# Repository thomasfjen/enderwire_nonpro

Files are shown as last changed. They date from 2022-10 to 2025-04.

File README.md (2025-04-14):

# Parts Collection

This is a collection of parts to make the DarkDog Rev2 Ender_SW compatible with the 2040 Y Extrusion of the original Ender.

Based on Gizzles Y-Axis https://github.com/VoronDesign/VoronUsers/tree/main/printer_mods/Gizzle/ender-3_pro_switchwire
  - The Motormount and chainmount are untouched the rest is redesigned for easier mounting with existing ender hardware and also added a tensioner for the belt.
  - There is an option to not drill the bed carriage plate and use the drillless bed carriage adapter (Folder Y-Axis -> Drilless Carriage) 

And DarkDogs Rev2 https://github.com/boubounokefalos/Ender_SW/tree/Rev.2
  - Most Parts of DarkDogs Rev2 are untouched (Get them from his Repo) and only a few edited files to make them fit (Check the table below)
  - My Y tensioner is based on DarkDogs desgin but completely redone to fit the 2040 extrusion and orientation of the belt.

There are mounts for the original PSU, the thick non-meanwell one.
It is advisable to not use a lower panel then (or create a cutout), as the psu fan is very close to the panel.

# Overview of changes:

- Y-axis extrusion moved forward one bolt hole with replacing one M5 bolt with shorter one and using a t-nut in the extrusion.
  35mm bolts are bit too long depending on how the extrusions are machined, so use some washers under the bolt head till the bolts 
  does not hit the bottom of the extrusion.
- Modified Skirt to hold PSU, added Parts when using original PSU.
- Located Pi to the front (less room in the back because of the vertical stepper), but you can get creative with electronics mounting/layout.
- Added a Y-Belt-Tensioner to the idler, similiar to DarkDogs desgin but completely redesigned to fit the 2040 extrusion and belt orientation
  You need to tap a M5 thread into the 2040 Y-Extrusion to mount the Y-Belt-tensioner. I simply used a cordless power drill and let the screw tap the thread itself since the aluminium is pretty soft.
  If you have a M5 Tap onhand using that is clearly the better method!

Majority of STL-Files are still from the DarkDog Conversion (boubounokefalos), basically everything except the Y-Axis Folder (Gantry -> Y-Axis Folder) and a few changed files (See table below)
https://github.com/boubounokefalos/Ender_SW/tree/main/STLS

You can use drill-less carriage adapter as drill template for mounting the linear rail carriage and chain mount to the bed plate or simply use the drill-less files.
You may have to use shorter bed springs/silicone spacers then, as the bed is raised about 8mm and can interfere with the lower z rail stops. There are smaller z_endstop files in the folder to reduce the problem as best as possible.

You may want to use the optimized motor mounts: https://github.com/strayr/SWE3-motor-mounts
They add a third screw to the frame to avoid tilting of the assembly.

As it was pretty expensive to source a keybak here in germany i used a mod to use a cheap door puller from aliexpress.
The 800gr version works great for me.
Door puller: https://www.aliexpress.com/item/1005001859337166.html 

Mount: https://github.com/kanawati975/Voron_Switchwire/tree/main/Key-Bak

Watch the Table down to see which files replace the DarkDogs files:
# Table of Parts to use instead of DarkDog files

| Part | Original | Replace with: | Comment: |
|---|---|---|---|
| Extension/Side Skirt | rear_extention_left_a | rear_extention_left_a_psu | Also replaces the PS_4040_Slide_Mount as mount for the psu |
| Deck Upper Side | deck_panel_left.dxf and [...] right.dxf| deck_upper_non_pro | Also available as dxf, Make sure you get it mirrored when getting cut if the material has two surface finishes (eg. glossy and structured)
| Rear Panel | rear_panel | rear_panel_non_pro | Also available as dxf |
|--------------------------------------------|-----------------------|---------------------------------------|------------------------------------------------------------|
| If using the original thick PSU: | | | |
|--------------------------------------------|-----------------------|---------------------------------------|------------------------------------------------------------|
| PSU Mount | PS_4040_mount_x2 | 2x orig_psu_mount | |
| Extension: | rear_extention_left_a | extension_left_a_orig_psu | |

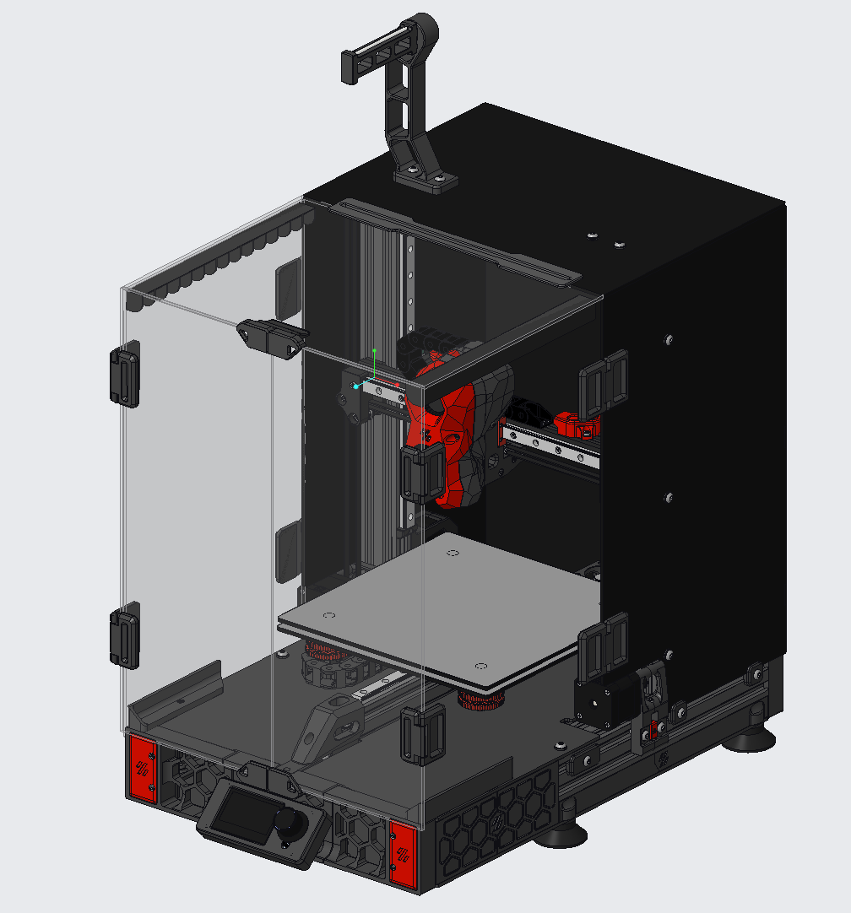
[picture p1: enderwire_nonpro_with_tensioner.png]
Home


If there are any questions/erros you can ping me in the ender_conversion_chat of the voron discord.
Cheers! 

# BOM 
RobotRogue did a great job creating a BOM for the Conversion: 
https://github.com/RobotRogue/Enderwire_Docs

For the Non-Pro you need one less linear rail (4 instead of 5).
For Y Idler / Tensioner you need a M3x25mm screw and nut, as well as a M5x20mm screw for the bearing stack.

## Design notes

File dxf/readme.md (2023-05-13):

Both Panel files are modified to fit the Non Pro Ender Frame. Use rest of dxf files from the Darkdog Rev 2 Github
When using a deck panel material with two different surface finishes make sure to mirror the dxf file to get the same surface finish on both parts.

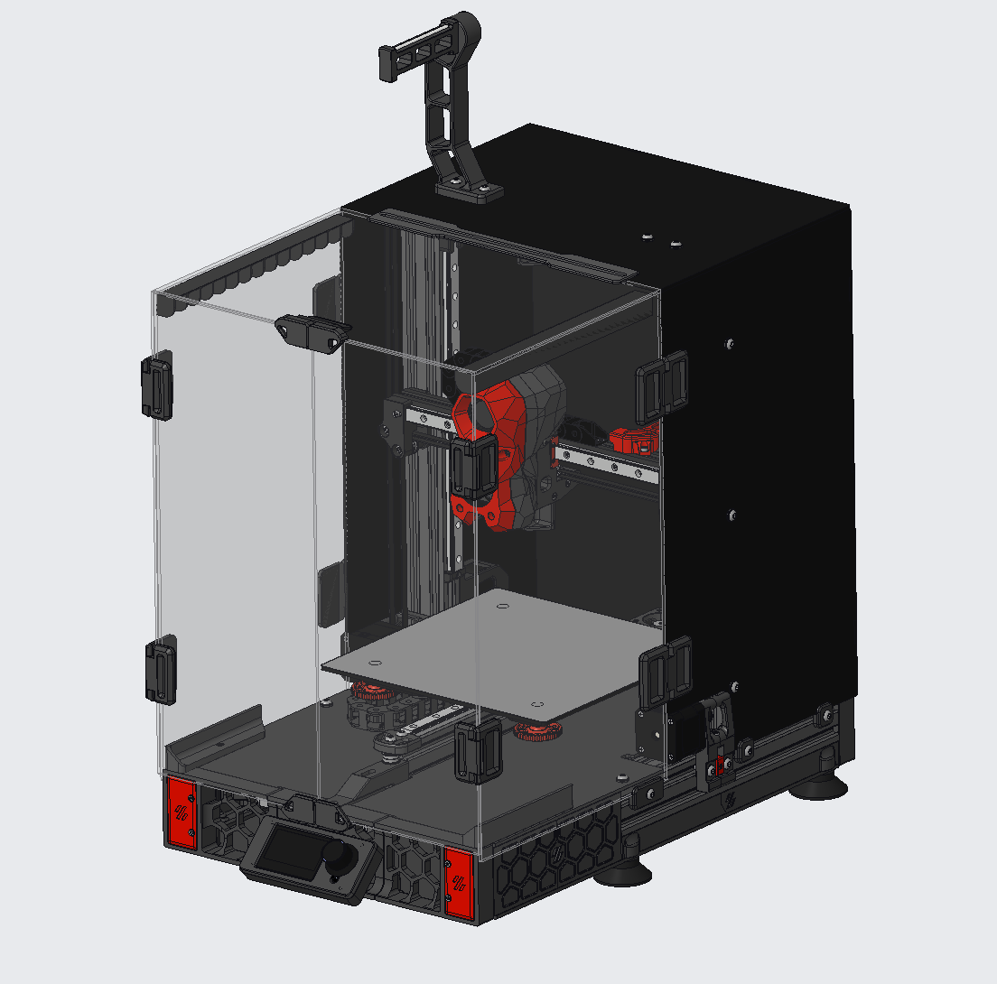
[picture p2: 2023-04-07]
enderwire_nonpro.png

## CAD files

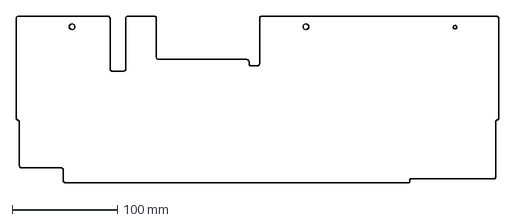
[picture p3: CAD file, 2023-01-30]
dxf/deck_upper_non_pro_fixed.dxf
458.0 x 158.0 mm

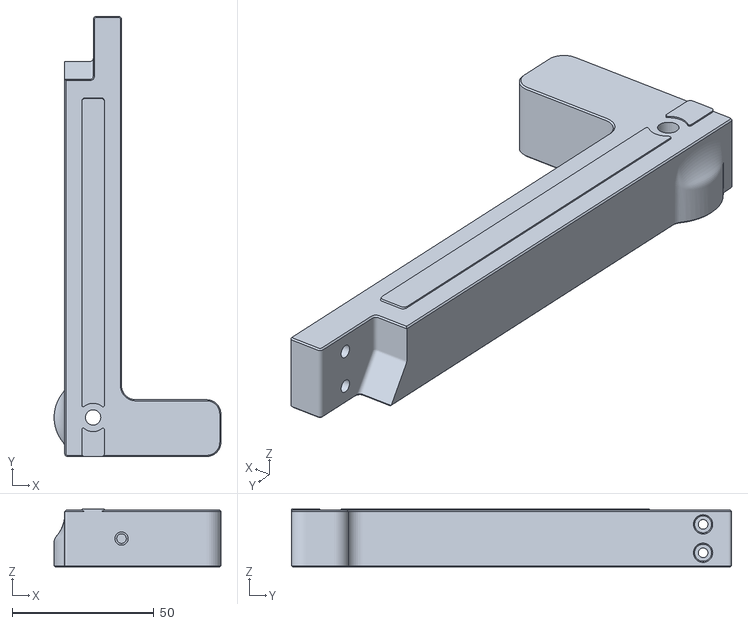
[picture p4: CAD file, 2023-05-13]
STLs/Extension/rear_extension_left_a_psu.stl
58.8 x 154.9 x 20.4

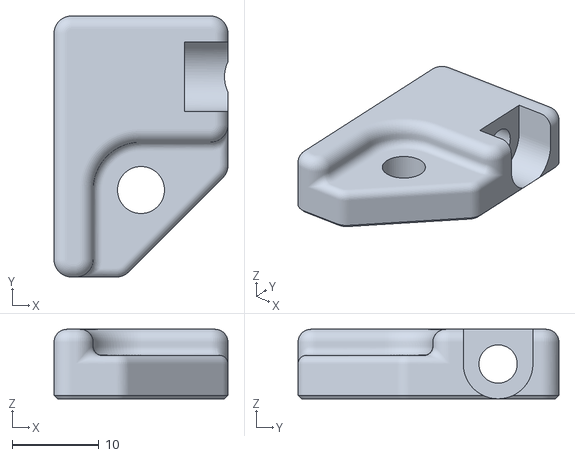
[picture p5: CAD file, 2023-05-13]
STLs/Original Thick PSU Mount/2xorig_psu_mount.stl
20.0 x 30.0 x 8.00

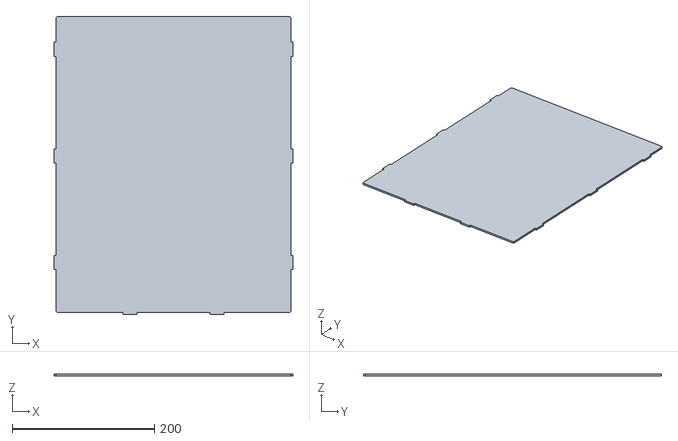
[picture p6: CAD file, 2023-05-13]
STLs/Panels/rear_panel_non_pro.stl
336.0 x 419.0 x 3.00

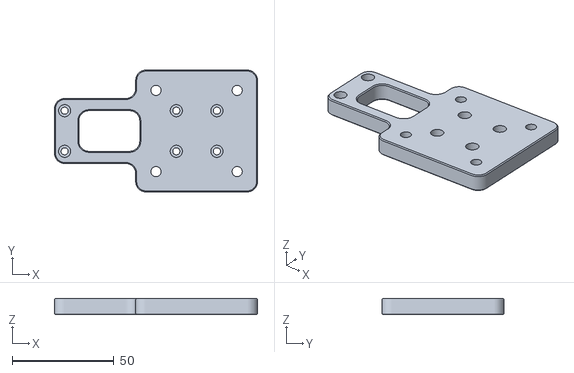
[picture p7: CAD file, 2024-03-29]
STLs/Y-Axis/bed_carriage_adapter.stl
100.0 x 60.0 x 8.00

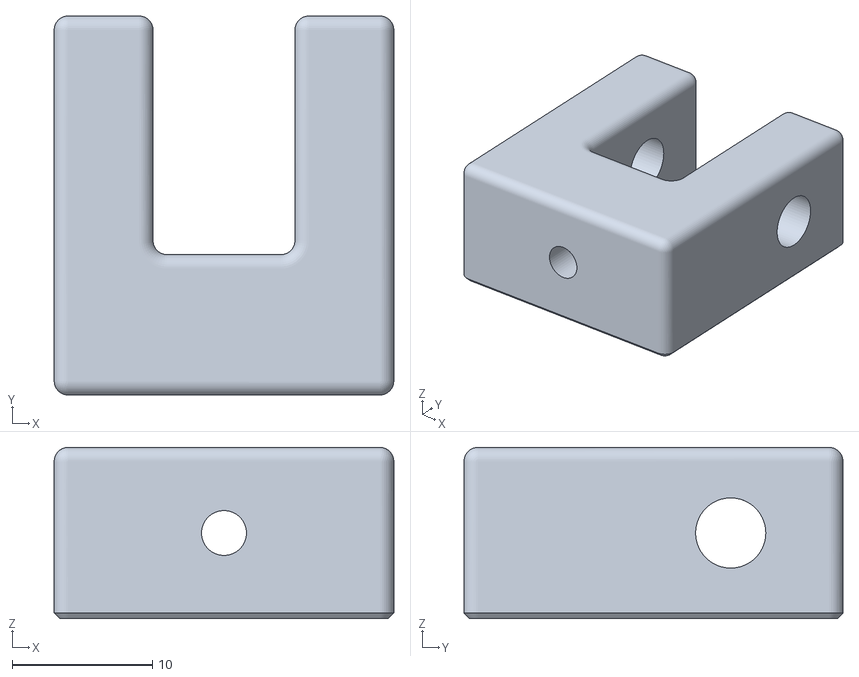
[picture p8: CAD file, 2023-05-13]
STLs/Y-Axis/Y-Idler_Tensioner/y_idler_inner.stl
24.2 x 27.0 x 12.2

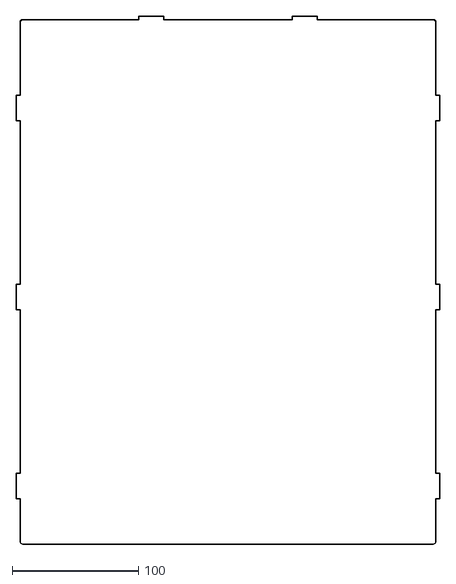
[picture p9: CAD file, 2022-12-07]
dxf/rear_panel_non_pro.dxf
336.0 x 419.0

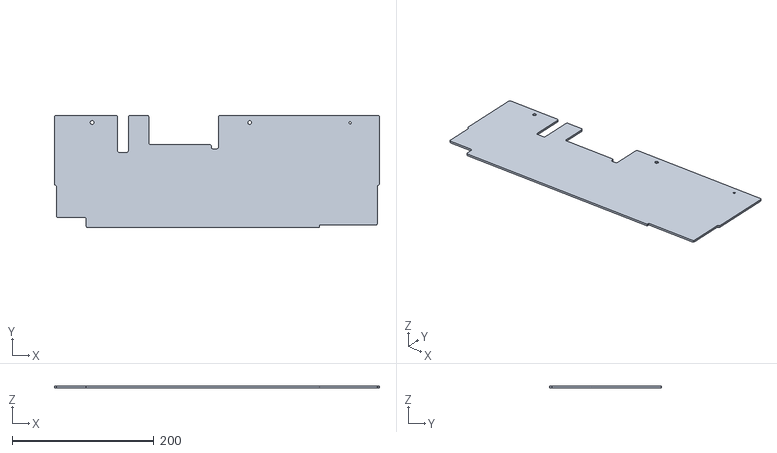
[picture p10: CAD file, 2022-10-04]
STLs/Panels/deck_upper_non_pro.stl
458.0 x 158.0 x 2.84

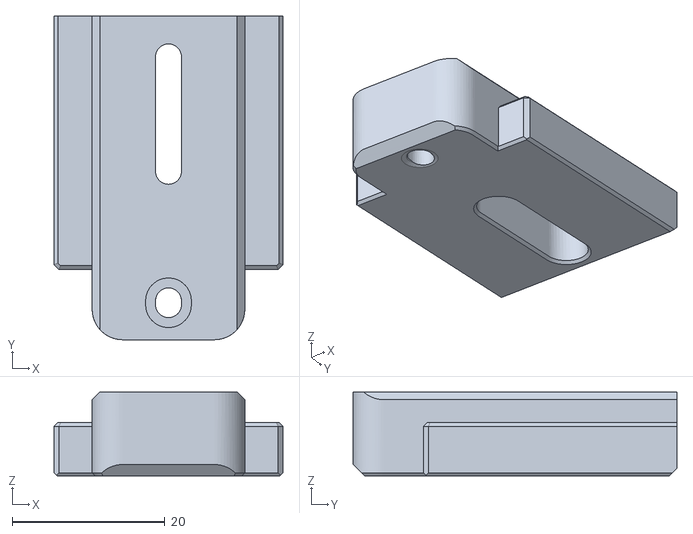
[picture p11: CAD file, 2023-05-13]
STLs/Y-Axis/Y-Idler_Tensioner/y_idler_b.stl
30.0 x 42.4 x 11.0

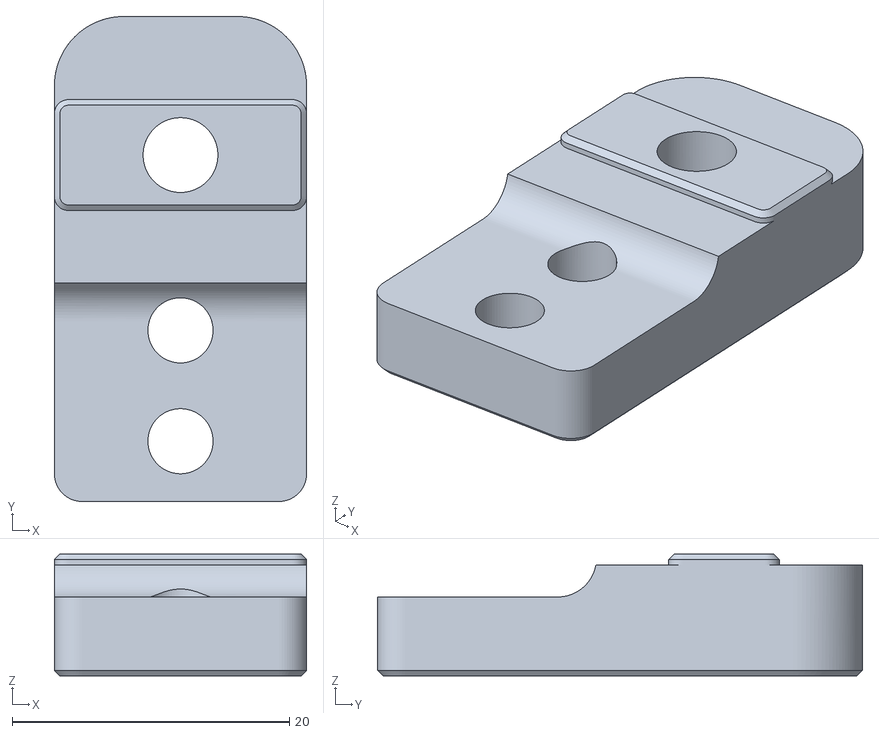
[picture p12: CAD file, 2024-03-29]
STLs/Y-Axis/y_chain_frame_mount_igus.stl
18.2 x 35.0 x 8.80

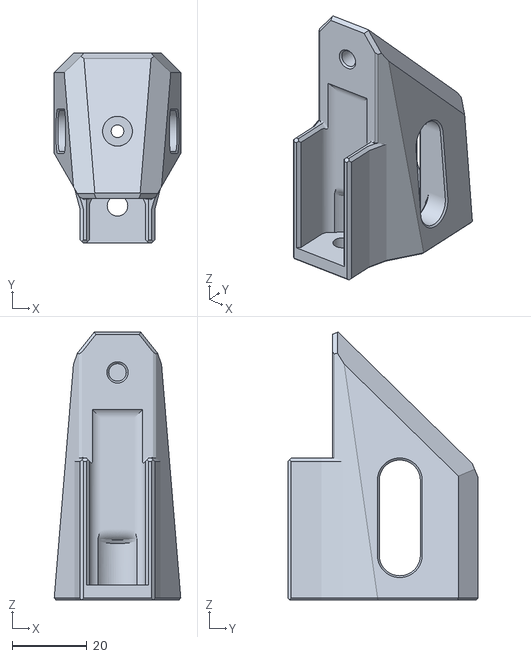
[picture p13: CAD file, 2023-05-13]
STLs/Y-Axis/Y-Idler_Tensioner/y_idler_a.stl
33.9 x 51.0 x 71.8

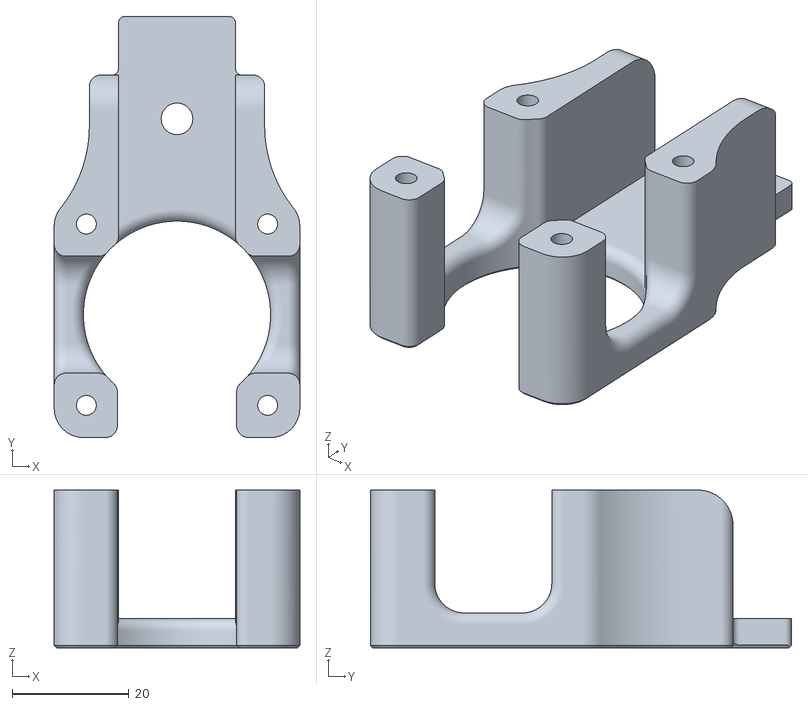
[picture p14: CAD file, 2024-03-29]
STLs/Y-Axis/y_motor_mount.stl
42.0 x 72.0 x 27.0

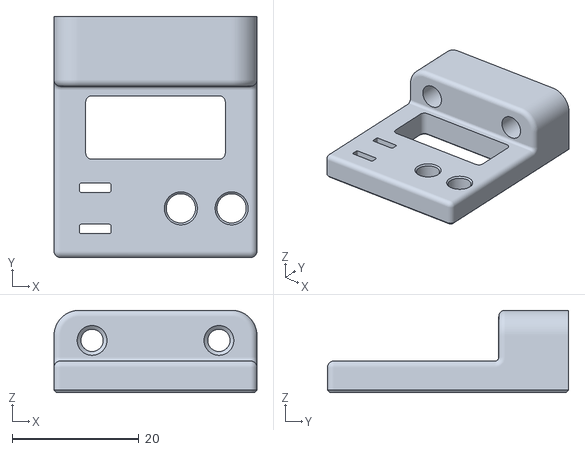
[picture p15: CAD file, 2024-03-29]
STLs/Y-Axis/y_chain_mount_igus.stl
32.0 x 38.0 x 13.0

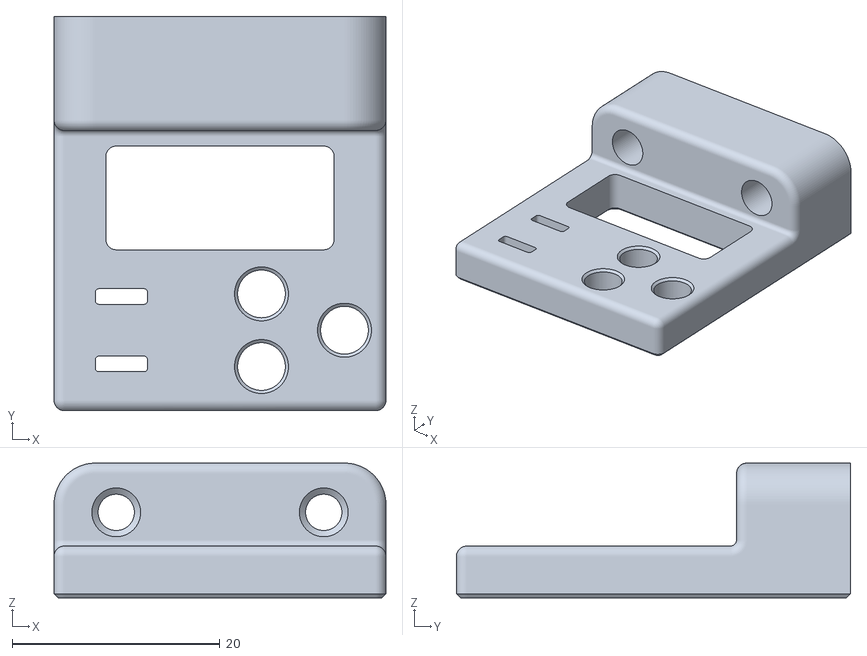
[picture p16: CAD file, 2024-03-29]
STLs/Y-Axis/y_chain_mount_generic.stl
32.0 x 38.0 x 13.0

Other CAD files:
STLs/Extension/rear_extension_a_psu.stl
STLs/Original Thick PSU Mount/rear_extension_left_a_orig_psu.stl
STLs/Y-Axis/y_chain_frame_mount_generic.stl
STLs/Y-Axis/z_carriage_stop_short.stl
STLs/Y-Axis/belt_anchor_bolt_on_plate.stl
STLs/Y-Axis/bolt_spacer_bed_plate.stl

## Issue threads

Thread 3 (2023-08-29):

Missing Y Part

Crstll, 2023-08-29:
Hi , where I found the extension for Y profile ?
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
Thanks :)

thomasfjen, 2023-08-29:
Hey!
That's not the up-to-date model anymore, it got updated with a belt tensioner.

If you want to use old model without y tensioner then you would need to export the model yourself.

Closed 2024-03-07.

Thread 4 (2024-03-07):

Minor discrepancies between bed_carriage_bolt_on.stl & enderwire_non_pro_asm.stp

thisiskeithb, 2024-03-07:
I wanted to add a 0.4mm chamfer to bottom face of `bed_carriage_bolt_on.stl` for improved printability, so I made the changes to `BED_PLATE_2` in `enderwire_non_pro_asm.stp` and exported the new model, but I noticed some minor discrepancies between what's in CAD and `bed_carriage_bolt_on.stl` provided in this repo.

The differences are minor, but they are not identical. Which is one is correct?

`BED_PLATE_2` from `enderwire_non_pro_asm.stp`:

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

Pre-exported `bed_carriage_bolt_on.stl`:

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

thomasfjen, 2024-03-07:
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

Hey! Yes there are some differences, i don't know what happend there or if i had a different revision at some point.

Checking my lasted files there are some minor differences and not exactly how i want it to be:
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

There is some play on one side when using the wheel holes, as the holes are bigger because of the excentric nuts and should cover the minor differences.

If i find time i'll fix the part and reupload the cad and stl.

thomasfjen, 2024-03-29:
I just fixed the thing you mentioned with the update:
https://github.com/thomasfjen/enderwire_nonpro/commit/a3b6391bcf7a07d493456b47ed8711a2c6669d34

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

Closed 2024-03-29.

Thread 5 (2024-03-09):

Y-Chain_Bed-Mount_x1 source missing from CAD?

thisiskeithb, 2024-03-09:
I'd like to remix [`Y-Chain_Bed-Mount_x1.stl`](https://github.com/thomasfjen/enderwire_nonpro/blob/main/STLs/Y-Axis/Y-Chain_Bed-Mount_x1.stl) to use a generic cable chain with "Igus" mounting holes (two inline holes vs. three in a triangular layout), but I don't see this part in `enderwire_non_pro_asm.stp`:

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

Note: I also checked in the [boubounokefalos/Ender_SW repo](https://github.com/boubounokefalos/Ender_SW), but [`[a]_y_chain_bed_mount_generic.stl`](https://github.com/boubounokefalos/Ender_SW/blob/main/STLS/Gantry/Y%20Axis/%5Ba%5D_y_chain_bed_mount_generic.stl) is completely different than what is hosted here.

thomasfjen, 2024-03-10:
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

You're right, looks that part went missing when exporting the STEP.
You can get it from the gizzle repo CAD :https://github.com/VoronDesign/VoronUsers/tree/master/printer_mods/Gizzle/ender-3_(pro)_switchwire

One thing more to add to my list.

thisiskeithb, 2024-03-10:
> You can get it from the gizzle repo CAD

Thanks! I should have looked there since it's called out in the README 😄

Having "generic" and "Igus" versions of `Y-Chain_Bed-Mount_x1.stl` & `Y-Chain_Frame-Mount_x1.stl` would be a nice improvement so this repo has a little more parity with the `boubounokefalos/Ender_SW` since both cable chain versions are available for Y & Z in that repo.

thomasfjen, 2024-03-29:
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

Added the igus variants:
https://github.com/thomasfjen/enderwire_nonpro/commit/a3b6391bcf7a07d493456b47ed8711a2c6669d34

If you have anymore issues let me know :)

Closed 2024-03-29.

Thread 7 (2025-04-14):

Modified rear grill missing

Mou-bit, 2025-04-14:
Hi im converting my ender to the switch wire and im printing out all the parts now but i read that theres a modified rear grill to work with the new Y motor position but i cant find it or maby im missing something please advise

thomasfjen, 2025-04-14:
Hello!
That's not needed anymore. You're right, i missed removing that from the gantry.

It's mentioned [here](https://github.com/thomasfjen/enderwire_nonpro/commit/a3b6391bcf7a07d493456b47ed8711a2c6669d34) that it's not needed anymore as the motor mount isn't used anymore for y tension as i added fron tensioner.

I'll update the readme so that's not mentioned anymore.
If you have any more question let me know :)

Mou-bit, 2025-04-14:
Thank you for the info and quick response
I knew i wasn't reading everything but thank you for the assistance and
great work on the conversation im learning a-lot on 3D design and modelling
thanks to how you incorporate other designs and modifying to works with the
non pro version

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

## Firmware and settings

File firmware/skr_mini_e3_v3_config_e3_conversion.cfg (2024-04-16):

## *** THINGS TO CHANGE/CHECK: ***
## MCU paths                         	[mcu] section
## Thermistor types                      [extruder] and [heater_bed] sections - See 'sensor types' list at end of file
## PID tune                              [extruder] and [heater_bed] sections
## Fine tune E steps                     [extruder] section

## For wiring directions please see https://docs.vorondesign.com/build/electrical/sw_miniE3_v20_wiring.html
## changed max positions on x,y,z to reflect the ender conversion and possible homing direction
## Also added screw_tilt_adjust section to use the screws_tilt_calculate macro
## Webclient config files. Uncomment one depending on UI being used.
#[include mainsail.cfg]
#[include fluidd.cfg] 

[printer]
kinematics: corexz
max_velocity: 200
max_accel: 1000
max_z_velocity: 50
max_z_accel: 1000
square_corner_velocity: 4.0

[mcu]
###Change to device found by "ls -l /dev/serial/by-id/" with just one this MCU connected to Pi
serial: /dev/serial/by-id/usb-Klipper_lpc1768_XXXXXXXXXXXXXXXXXXXXX

[static_digital_output usb_pullup_enable]
pins: !PC13

#####################################################################
# 	X Stepper Settings
#####################################################################

######
# Motor -XM
# Endstop - X-STOP
###############
[stepper_x]
step_pin: PB13
dir_pin: PB12
enable_pin: !PB14
rotation_distance: 40
full_steps_per_rotation: 200
microsteps: 32
endstop_pin: ^PC0
position_endstop: 220
position_min: 0
position_max: 220
homing_speed: 40
homing_positive_dir: true

[tmc2209 stepper_x]
uart_pin: PC11
tx_pin: PC10
uart_address: 0
run_current: 0.5
interpolate: False
stealthchop_threshold: 0

#####################################################################
#   Y Stepper Settings
#####################################################################

######
# Motor -YM
# Endstop - Y-STOP
###############
[stepper_y]
step_pin: PB10
dir_pin: PB2
enable_pin: !PB11
rotation_distance: 40
full_steps_per_rotation: 200
microsteps: 32
position_min: 0
position_max: 235
homing_speed: 40

## Uncomment one of the following:
## Switch-based endstop for Y
#endstop_pin: ^PC1 

##Switch and the end of the Y Extrusion:
#position_endstop: 0

##Switch on the Bed Belt Clamp:
#position_endstop: 235
#homing_positive_dir: true

## Sensorless endstop for Y
#endstop_pin: tmc2209_stepper_y:virtual_endstop
#homing_retract_dist: 0 # Uncomment this line too
#position_endstop: 235 # Uncomment this line too


[tmc2209 stepper_y]
uart_pin: PC11
tx_pin: PC10
uart_address: 2
run_current: 0.5
interpolate: False
stealthchop_threshold: 0
## Uncomment if using sensorless Y homing.
#driver_SGTHRS: 120 # tune this once it's working.

#####################################################################
# 	Z Stepper Settings
#####################################################################

######
# Motor -ZAM
# Endstop - Z-STOP
###############
[stepper_z]
step_pin: PB0
dir_pin: PC5
enable_pin: !PB1
rotation_distance: 40
full_steps_per_rotation: 200
microsteps: 32
endstop_pin: probe:z_virtual_endstop
##conversative max_z 
position_max: 200
homing_speed: 40
position_min: -3.0

[tmc2209 stepper_z]
uart_pin: PC11
tx_pin: PC10
uart_address: 1
run_current: 0.5
interpolate: False
stealthchop_threshold: 0

#####################################################################
#   Extruder Settings
#####################################################################

######
#Motor - EM
###############
[extruder]
# E0_STEP_PIN        PB3
# E0_DIR_PIN         PB4
# E0_ENABLE_PIN      PB1
# E0_UART_RX         PC11
# E0_UART_TX         PC10
step_pin: PB3
dir_pin: PB4
enable_pin: !PD1
##  Update value below when you perform extruder calibration
##  If you ask for 100mm of filament, but in reality it is 98mm:
##  rotation_distance = <previous_rotation_distance> * <actual_extrude_distance> / 100
##  22.6789511 is a good starting point
rotation_distance: 22.6789511   #Bondtech 5mm Drive Gears
##  Update Gear Ratio depending on your Extruder Type
##  Use 50:10 for Stealthburner/Clockwork 2
##  Use 50:17 for Afterburner/Clockwork (BMG Gear Ratio)
##  Use 80:20 for M4, M3.1
gear_ratio: 50:10
microsteps: 32
full_steps_per_rotation: 200
nozzle_diameter: 0.400
filament_diameter: 1.75
heater_pin: PC8
##  Validate the following thermistor type to make sure it is correct
##  See https://www.klipper3d.org/Config_Reference.html#common-thermistors for additional options
# sensor_type: Generic 3950
sensor_pin: PA0
min_temp: 10
max_temp: 270
max_power: 1.0
min_extrude_temp: 170
control = pid
pid_kp = 26.213
pid_ki = 1.304
pid_kd = 131.721
#Set appropriate once tuning your printer
#pressure_advance: .05
##	Default is 0.040, leave stock
# pressure_advance_smooth_time: 0.040
max_extrude_only_distance: 100.0

[tmc2209 extruder]
uart_pin: PC11
tx_pin: PC10
uart_address: 3
run_current: 0.7
hold_current: 0.3
interpolate: False

#####################################################################
# 	Bed Heater
#####################################################################

######
# BED Connector
###############
[heater_bed]
heater_pin: PC9
##  Validate the following thermistor type to make sure it is correct
##  See https://www.klipper3d.org/Config_Reference.html#common-thermistors for additional options
# sensor_type: Generic 3950
sensor_pin: PC4
min_temp: 0
max_temp: 130
control: pid
pid_kp: 58.437
pid_ki: 2.347
pid_kd: 363.769

#####################################################################
# 	Probe
#####################################################################

######
#Z Max Connector on Z(main) Board
#Inductive Probe
###############
[probe]
##      If your probe is NO instead of NC, add change pin to !z:P1.24
pin: ^PC2
x_offset: 0
y_offset: 25
z_offset: 0
samples: 3
samples_result: median
sample_retract_dist: 3
samples_tolerance: 0.006
samples_tolerance_retries: 3

#####################################################################
# 	Fan Control
#####################################################################

######
# Electronics Fan
# FAN1 Connector
###############
[controller_fan my_controller_fan]
pin: PC7 
max_power: 1.00
kick_start_time: 0.200
heater: heater_bed

######
# Hot End Fan
# FAN2 Connector
###############
[heater_fan extruder_fan]
pin: PB15
heater: extruder
heater_temp: 50.0
##  If you are experiencing back flow, you can reduce fan_speed
#fan_speed: 1.0

######
# Part Cooling Fan
# FAN0 Connector
###############
[fan]
pin: PC6  # "FAN0"
cycle_time: .08
##	Depending on your fan, you may need to increase this value
##	if your fan will not start. Can change cycle_time (increase)
##	if your fan is not able to slow down effectively
kick_start_time: .25

#####################################################################
#   Homing, Bed Mesh and Screw Tilt adjust
#####################################################################
[homing_override]
axes: z
set_position_z: 0
gcode:
    G90
    G0 Z5 F500
    G28 X0 Y0
    G0 X110 Y100 F9000
    G28 Z0
    G0 Z5 F500

[bed_mesh]
speed: 150
horizontal_move_z: 5
mesh_min: 2,0
mesh_max: 218,200
probe_count: 6,6
algorithm: bicubic
fade_start: 1
fade_end: 10
fade_target: 0


[screws_tilt_adjust]
screw1: 195, 180
screw1_name: rear right screw
screw2: 25, 180
screw2_name: rear left screw
screw3: 25, 10
screw3_name: front left screw
screw4: 195, 10
screw4_name: front right screw
horizontal_move_z: 15.
speed: 50.
screw_thread: CW-M4

#####################################################################
# 	Displays
#####################################################################
## 	For the mini12864 Display, the [display] and [neopixel] must be uncommented
# mini12864 LCD Display
# connected to exp1/2
#[display]
##    mini12864 LCD Display
#lcd_type: uc1701
#cs_pin: PB8
#a0_pin: PB15
#rst_pin: PB9
#encoder_pins: ^PA9,^PA10
#click_pin: ^!PB5
#contrast: 63
#spi_software_sclk_pin: PA5
#spi_software_mosi_pin: PA7
#spi_software_miso_pin: PA6
#menu_reverse_navigation: True

#[neopixel fysetc_mini12864]
##	To control Neopixel RGB in mini12864 display
## Remember with these ones, you'll need to remove the connector header on the LCD for EXT1 + 2
## (it slides off) and reverse it for it to work on your SKR (1.3 and 1.4) board
#pin: PA15
#chain_count: 3
#initial_RED: 1
#initial_GREEN: 1
#initial_BLUE: 1
#color_order: RGB

##	Set RGB values on boot up for each Neopixel. 
##	Index 1 = display, Index 2 and 3 = Knob
#[delayed_gcode setdisplayneopixel]
#initial_duration: 1
#gcode:
#        SET_LED LED=fysetc_mini12864 RED=1 GREEN=1 BLUE=1 INDEX=1 TRANSMIT=0	# Backlit Screen colour
#        SET_LED LED=fysetc_mini12864 RED=1 GREEN=0 BLUE=0 INDEX=2 TRANSMIT=0	# Top left Knob colour
#        SET_LED LED=fysetc_mini12864 RED=1 GREEN=0 BLUE=0 INDEX=3				# Bottom right knob colour
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

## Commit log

2022-09-23 0.2 Update
    Y-Axis (Idler + Connection piece) conntected to front grill,
    Deck Panels modifed to fit single 2040 y extrusion.
    Added Panles to STEP Filled hole of Rear Panel
2022-10-04 add STLs for modified parts
    [deck_upper.stl, front_y_grill_connection.stl, grill_rear_middle.stl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]
2022-10-14 psu_mount_original
    added psu mount for the original psu mount
    [orig_psu_mount.stl]
2022-10-14 Original PSU Mount
    Mount for orignal thick PSU Mount
    [orig_psu_mount.stl]
2022-10-27 smaller diameter idler bolt
    reduced the diameter for the idler bolt to cut a thread when inserting the bolt.
    First version still works fine for me
    [front_y_grill_connection_thread.stl]
2022-12-07 add dxf files
    [deck_upper.dxf, rear_panel.dxf]
2022-12-07 dxf update sheet dimension
    [deck_upper.dxf, rear_panel.dxf]
2022-12-23 Update Name
    [grill_rear_middle_non_pro.stl]
2022-12-23 update names
    [deck_upper_non_pro.dxf, rear_panel_non_pro.dxf]
2022-12-23 Update Step
    added missing Railstops on Z
2023-01-30 fixed file and removed drawing frame
    [deck_upper_non_pro_fixed.dxf]
2023-02-17 added belt anchor
    Belt anchor with holes for m5 screws and m5 self locking nuts from the wheels
    [belt_anchor_m5.stl]
2023-02-21 More Clearance for moving the y axis
    [front_y_grill_connection_v2.stl]
2023-02-23 Added drill-less carriage
    Added a plate to mounting the carraige to the rail without drilling it
    [bed_carriage_bolt_on.stl, belt_anchor_bolt_on_plate.stl, bolt_spacer_bed_plate.stl]
2023-02-23 Clearance Bed
    Adds 6mm more clearance from the bed to the carriage stop
    [z_carriage_stop_short.stl]
2023-03-02 added psu embossing in printed part
    [rear_extension_a_psu.stl]
2023-04-07 CAD Update Reference to Release Version 2
    Updated the CAD to Release Version 2 by Darkdog.
    Added the bolt carriage to the cad and fixed the orientation
2023-04-07 update CAD and Picture
2023-04-13 BOM Update
    Added Link to Robotrogue BOM
2023-05-13 Tensioner, Parts orientation
    Added Y-Belt tensioner
    Changed orientation of Parts to printing orientation
    [2xorig_psu_mount.stl, Y-Chain_Frame-Mount_x1.stl, belt_anchor_bolt_on_plate.stl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]
2023-05-14 Update CAD
    Updated the cad with Tensioner
2023-05-16 CAD Update
    Corrected Orientation and Colours to include into Export
2023-05-19 Update README.md
    Added Extrusion Tapping for Y-Idler Info
2023-05-19 Update README.md
    Update Info to use drillless adapter as drill guide of bed plate
2023-05-19 Keybak Alternative added
    Added Link of Keybak alternative and mount
2023-06-22 Missing Belt Clamp
    Upload missing belt clamp
2023-08-19 Add firmware
    Example config from switchwire preconfigured for e3 conversion
    [skr_mini_e3_v3_config_e3_conversion.cfg]
2023-08-19 Ender Bed_Mesh and Screw_tilt_adjust
    Added ender specific bed mesh max and mins and added screw tilt adjust section to be able to level the bed with the probe
    [skr_mini_e3_v3_config_e3_conversion.cfg]
2024-03-29 Various fixes/additions to clean up
    - redesigned bed plate to fix odd dimensions
    - redesigned y chain mount to add igus variant
    - added frame chain mount igus variant
    - added railstopper on motor mount-> no risk of the carraige moving from the rail
    -updated cad
    -removed rear grill (not necessary anymore as motor mount isn't used for tensioning anymore), connection piece to tbd
    -fixed dimensions of hex nut hole in belt anchor to prevent splitting
    -streamlined bolt on vs direct mount of bed plate, no reason to have two versions
    -updated cad
    [Y-Chain_Frame-Mount_x1.stl, bed_carriage_adapter.stl, bed_carriage_bolt_on.stl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]
2024-04-16 Update skr_mini_e3_v3_config_e3_conversion.cfg
    update mesh and homing sequence
    [skr_mini_e3_v3_config_e3_conversion.cfg]
2024-04-16 reduce homing speed
    homing_positive_dir: true
    [skr_mini_e3_v3_config_e3_conversion.cfg]
